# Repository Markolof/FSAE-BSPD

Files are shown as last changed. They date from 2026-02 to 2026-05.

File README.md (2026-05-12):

BSPD with SCS — MES Racing
Rev 2.0 | Formula Student Rule Compliant
Brake System Plausibility Device with Short Circuit Sense. Opens the shutdown circuit if brake and motor current are simultaneously active for more than 0.5 seconds.
Key ICs

LM293 × 4 — comparators (brake & current thresholds)
NE555 — 0.5s timing
SN74HC27 — fault logic
LM358 — buffering
uA7805 — 5V regulation

Adjustable Thresholds
RV1/RV2 — brake | RV3/RV4/RV5 — current

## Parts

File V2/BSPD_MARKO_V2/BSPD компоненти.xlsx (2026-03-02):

v C1, C2, C11, C14, C18 | 5 | 10n | https://www.loging.mk/1478/197583/0/ShowProduct/Kondenzator |  | 110
C1 | 1 | 10n
C2 | 1 | 10n
C11 | 1 | 10n
C14 | 1 | 10n
C18 | 1 | 10n
C3 | 1 | 330n | https://www.loging.mk/1478/169780/0/ShowProduct/Kondenzator_ |  | 13
C4 | 1 | 100n | https://www.loging.mk/1478/197581/0/ShowProduct/Kondenzator |  | 140
> C5, C6, C9, C13, C15, C16 | 6 | 100n
> C7, C8 | 2 | 15p | https://www.loging.mk/1479/199631/0/ShowProduct/Keramichki_Kondenzator |  | 10
C10 | 1 | 15u | https://www.loging.mk/1207/172544/0/ShowProduct/Tantal_Kondenzator_ |  | 47
> C12, C17 | 2 | 10u | https://www.loging.mk/1476/167584/0/ShowProduct/Elektrolitski_Kondenzator_ |  | 28
D1 | 1 | B120-E3 | https://www.loging.mk/1354/162240/0/ShowProduct/Dioda |  | 3
D2 | 1 | 1N4148 | https://www.loging.mk/1354/162242/0/ShowProduct/Dioda |  | 2
> D3-D5 | 3 | 1N5822 | https://www.loging.mk/1548/166237/0/ShowProduct/Shotki_Dioda |  | 18
D7 | 1 | 1N4007 | https://www.loging.mk/1354/162240/0/ShowProduct/Dioda |  | 3
D8 | 1 | CDBA340-HF | https://www.loging.mk/1548/166237/0/ShowProduct/Shotki_Dioda |  | 18
> H1-H4 | 4 | MountingHole
> H5-H8 | 4 | MountingHole
J1 | 1 | ED555_8DS |  | Сликај од старо BSPD терминали за заштрафување
> J2-J4 | 3 | Conn_01x01_Pin |  | Сликај од старо BSPD терминали за заштрафување
J5 | 1 | Conn_01x01_Pin |  | Сликај од старо BSPD терминали за заштрафување
K1 | 1 | SANYOU_SRD_Form_C |  | https://www.loging.mk/1429/173069/0/ShowProduct/Rele | 145
Q1 | 1 | PMOS | https://www.loging.mk/1391/176659/0/ShowProduct/P-Kanalen__MOSFET |  | 215
> R1, R2, R19, R27, R34, R39 | 6 | 1k | https://www.loging.mk/1486/187132/0/ShowProduct/Otpornik_2W |  | 30
> R3, R4, R7, R9, R11, R16, R17, R21, R22, R24, R26, R29, R30 | 13 | 100k | https://www.loging.mk/1482/194923/0/ShowProduct/Otpornik_1_2W |  | 39
> R5, R6, R23, R31 | 4 | 51k | https://www.loging.mk/1483/186442/0/ShowProduct/Otpornik_1_4W |  | 4
> R8, R10, R12-R15, R18, R25, R28, R32, R33, R35-R37 | 14 | 10k | https://www.loging.mk/1484/185622/0/ShowProduct/Otpornik_1_4W |  | 28
R20 | 1 | 910k | https://www.loging.mk/1484/186593/0/ShowProduct/Otpornik_1_4W |  | 2
> RV1-RV5 | 5 | 100k | https://www.loging.mk/1484/186875/0/ShowProduct/Otpornik_1_4W |  | 10
> TP1, TP4 | 2 | TestPoint
U1 | 1 | uA7805 | https://www.loging.mk/1590/164528/0/ShowProduct/Regulator_na_Napon_ |  | 25
> U2-U4, U6 | 4 | LM293_COMP | https://www.loging.mk/1582/163629/0/ShowProduct/Operaciski_Zasiluvach_ |  | 80
U5 | 1 | SN74HC27NE4 | https://www.loging.mk/1594/168179/0/ShowProduct/NILI_Porta |  | 42
U7 | 1 | NE555N | https://www.loging.mk/1567/163760/0/ShowProduct/RC_Tajmer_ |  | 25
ВКУПНО |  |  |  |  | 1037

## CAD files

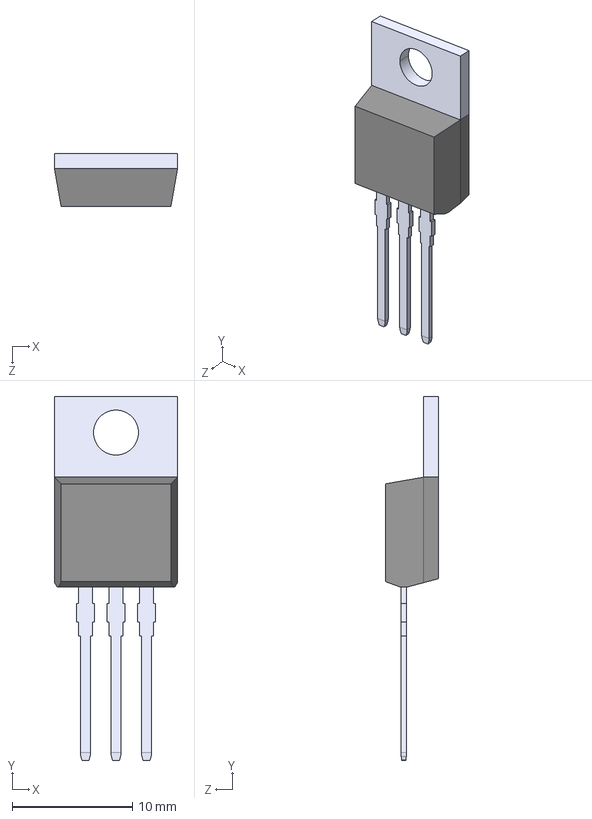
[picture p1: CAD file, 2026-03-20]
BSPD_MES_RACING_V3/Snapeda downloads/IRF9540/IRF9540.step
10.2 x 30.3 x 4.44 mm

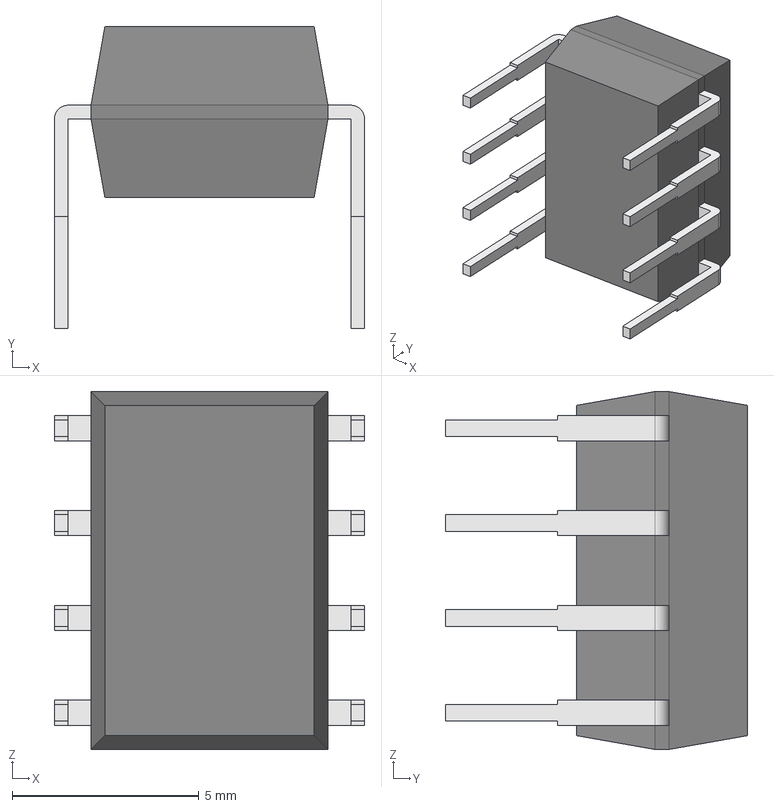
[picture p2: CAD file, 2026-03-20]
BSPD_MES_RACING_V3/Snapeda downloads/LM358N_NOPB/LM358N_NOPB.step
8.31 x 8.08 x 9.59 mm
Body001 (Mirror #1) x 5

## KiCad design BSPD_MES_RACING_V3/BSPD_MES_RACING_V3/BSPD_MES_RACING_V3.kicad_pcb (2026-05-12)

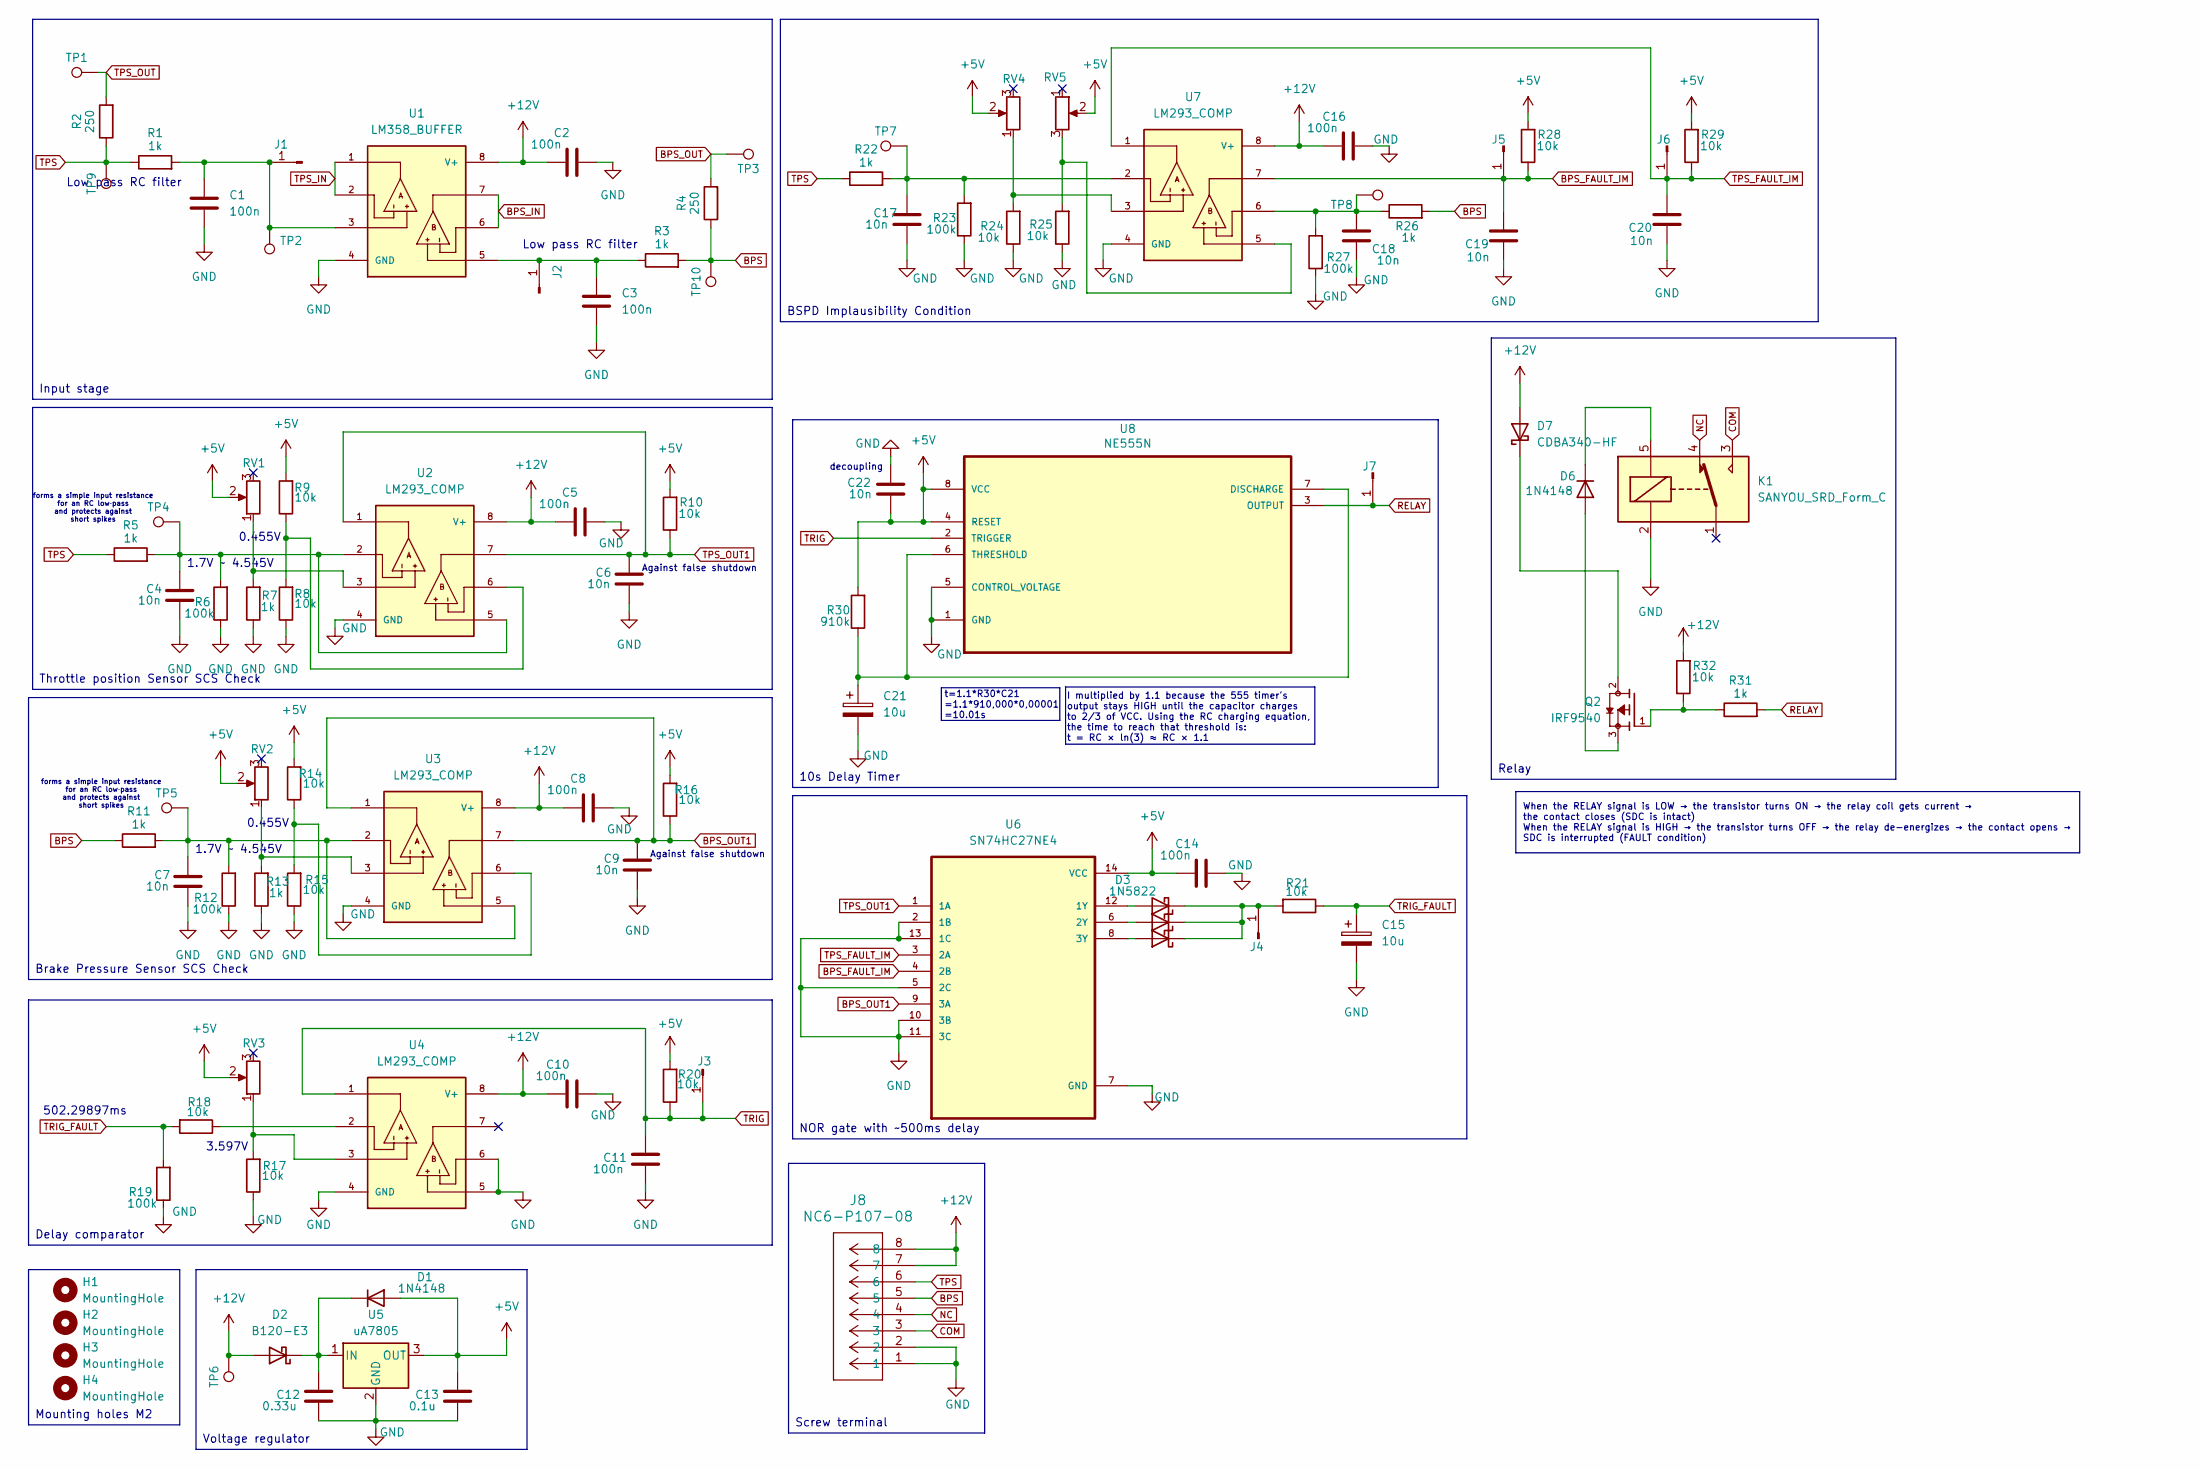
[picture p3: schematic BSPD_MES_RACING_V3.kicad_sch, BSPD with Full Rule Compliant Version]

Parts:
C1, C2, C3, C5, C8, C10, C11, C14, C16: 100n; Resonator-2Pin_W7.0mm_H2.5mm
C4, C6, C7, C9, C17, C18, C19, C20, C22: 10n; Resonator-2Pin_W7.0mm_H2.5mm
C12: 0.33u; Resonator-2Pin_W7.0mm_H2.5mm
C13: 0.1u; Resonator-2Pin_W7.0mm_H2.5mm
C15, C21: 10u; CP_Radial_D8.0mm_P5.00mm
D1, D6: 1N4148; D_DO-35_SOD27_P7.62mm_Horizontal
D2: B120-E3; D_DO-201AE_P15.24mm_Horizontal
D3, D4, D5: 1N5822; D_DO-201AD_P15.24mm_Horizontal
D7: CDBA340-HF; D_DO-201AE_P15.24mm_Horizontal
H1, H2, H3, H4: MountingHole; MountingHole_2.2mm_M2
J1, J2, J3, J4, J5, J6, J7: Conn_01x01_Pin; PinHeader_1x01_P2.54mm_Vertical
J8: NC6-P107-08; CONN8_NC6-P107-08_TEC
K1: SANYOU_SRD_Form_C; Relay_SPDT_SANYOU_SRD_Series_Form_C
Q2: IRF9540; TO254P1052X465X1989-3; PARTREV B
R1, R3, R5, R7, R11, R13, R22, R26, R31: 1k; R_Axial_DIN0207_L6.3mm_D2.5mm_P10.16mm_Horizontal
R2, R4: 250; R_Axial_DIN0207_L6.3mm_D2.5mm_P10.16mm_Horizontal
R6, R12, R19, R23, R27: 100k; R_Axial_DIN0207_L6.3mm_D2.5mm_P10.16mm_Horizontal
R8, R9, R10, R14, R15, R16, R17, R18, R20, R21, R24, R25, R28, R29, R32: 10k; R_Axial_DIN0207_L6.3mm_D2.5mm_P10.16mm_Horizontal
R30: 910k; R_Axial_DIN0207_L6.3mm_D2.5mm_P10.16mm_Horizontal
RV1, RV2, RV3, RV4, RV5: 100k; Potentiometer_Bourns_3266Y_Vertical
TP1, TP2, TP3, TP4, TP5, TP6, TP7, TP8, TP9, TP10: TestPoint; TestPoint_Pad_4.0x4.0mm
U1: LM358_BUFFER; DIP794W45P254L959H508Q8
U2, U3, U4, U7: LM293_COMP; DIP794W45P254L959H508Q8
U5: uA7805; TO-220-3_Horizontal_TabDown
U6: SN74HC27NE4; CERDIP-14_W7.62mm_SideBrazed_LongPads_Socket
U8: NE555N; CERDIP-8_W7.62mm_SideBrazed_LongPads_Socket; MPN NE555N

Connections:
+5V: C13.2, C14.1, C22.2, D1.2 (A), R9.2, R10.2, R14.2, R16.2, R20.2, R28.2, R29.2, R30.2, RV1.2, RV2.2, RV3.2, RV4.2, RV5.2, U5.3 (OUT), U6.14 (VCC), U8.4 (RESET), U8.8 (VCC)
+12V: C2.1, C5.1, C8.1, C10.1, C16.1, D2.2 (A), D7.2 (A), J8.7, J8.8, R32.2, TP6.1, U1.8 (V+), U2.8 (V+), U3.8 (V+), U4.8 (V+), U7.8 (V+)
BPS: J8.5, R3.2, R4.1, R11.1, R26.2, TP10.1
BPS_FAULT_IM: C19.1, J5.1, R28.1, U6.4 (2B), U7.7
BPS_IN: U1.6, U1.7
BPS_OUT: R4.2, TP3.1
BPS_OUT1: C9.1, R16.1, U3.1, U3.7, U6.9 (3A)
COM: J8.3, K1.3
GND: C1.2, C2.2, C3.2, C4.2, C5.2, C6.2, C7.2, C8.2, C9.2, C10.2, C11.1, C12.1, C13.1, C14.2, C15.2, C16.2, C17.2, C18.2, C19.2, C20.2, C21.2, C22.1, J8.1, J8.2, K1.2, R6.1, R7.1, R8.1, R12.1, R13.1, R15.1, R17.1, R19.1, R23.1, R24.1, R25.1, R27.1, U1.4 (GND), U2.4 (GND), U3.4 (GND), U4.4 (GND), U4.5, U4.6, U5.2 (GND), U6.2 (1B), U6.5 (2C), U6.7 (GND), U6.10 (3B), U6.11 (3C), U6.13 (1C), U7.4 (GND), U8.1 (GND), U8.5 (CONTROL_VOLTAGE)
NC: J8.4, K1.4
unnamed: C4.1, R5.2, R6.2, TP4.1, U2.2, U2.5
unnamed: C7.1, R11.2, R12.2, TP5.1, U3.2, U3.5
unnamed: C17.1, R22.2, R23.2, TP7.1, U7.2
unnamed: C18.1, R26.1, R27.2, TP8.1, U7.6
unnamed: C12.2, D1.1 (K), D2.1 (K), U5.1 (IN)
unnamed: D3.2 (A), U6.12 (1Y)
unnamed: D3.1 (K), D4.1 (K), D5.1 (K), J4.1, R21.2
unnamed: D4.2 (A), U6.6 (2Y)
unnamed: D5.2 (A), U6.8 (3Y)
unnamed: D6.2 (A), Q2.3
unnamed: D6.1 (K), K1.5
unnamed: D7.1 (K), Q2.2
unnamed: C1.1, J1.1, R1.2, TP2.1, U1.3
unnamed: C3.1, J2.1, R3.1, U1.5
unnamed: Q2.1, R31.1, R32.1
unnamed: R7.2, RV1.1, U2.3
unnamed: R8.2, R9.1, U2.6
unnamed: R13.2, RV2.1, U3.3
unnamed: R14.1, R15.2, U3.6
unnamed: R17.2, RV3.1, U4.3
unnamed: R18.1, U4.2
unnamed: R24.2, RV4.1, U7.3
unnamed: R25.2, RV5.3, U7.5
unnamed: C21.1, R30.1, U8.6 (THRESHOLD), U8.7 (DISCHARGE)
RELAY: J7.1, R31.2, U8.3 (OUTPUT)
TPS: J8.6, R1.1, R2.1, R5.1, R22.1, TP9.1
TPS_FAULT_IM: C20.1, J6.1, R29.1, U6.3 (2A), U7.1
TPS_IN: U1.1, U1.2
TPS_OUT: R2.2, TP1.1
TPS_OUT1: C6.1, R10.1, U2.1, U2.7, U6.1 (1A)
TRIG: C11.2, J3.1, R20.1, U4.1, U8.2 (TRIGGER)
TRIG_FAULT: C15.1, R18.2, R19.2, R21.1

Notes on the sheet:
3.597V
When the RELAY signal is LOW → the transistor turns ON → the relay coil gets current → the contact closes (SDC is intact) When the RELAY signal is HIGH → the transistor turns OFF → the relay de-energizes → the contact opens → SDC is interrupted (FAULT condition)
forms a simple input resistance for an RC low‑pass and protects against short spikes
502.29897ms
0.455V
Low pass RC filter
I multiplied by 1.1 because the 555 timer's output stays HIGH until the capacitor charges to 2/3 of VCC. Using the RC charging equation, the time to reach that threshold is: t = RC × ln(3) ≈ RC × 1.1
Against false shutdown
t=1.1*R30*C21 =1.1*910,000*0,00001 =10.01s
1.7V ~ 4.545V
decoupling
Relay
NOR gate with ~500ms delay
Screw terminal
Brake Pressure Sensor SCS Check
Throttle position Sensor SCS Check
Input stage
10s Delay Timer
BSPD Implausibility Condition
Voltage regulator
Mounting holes M2
Delay comparator

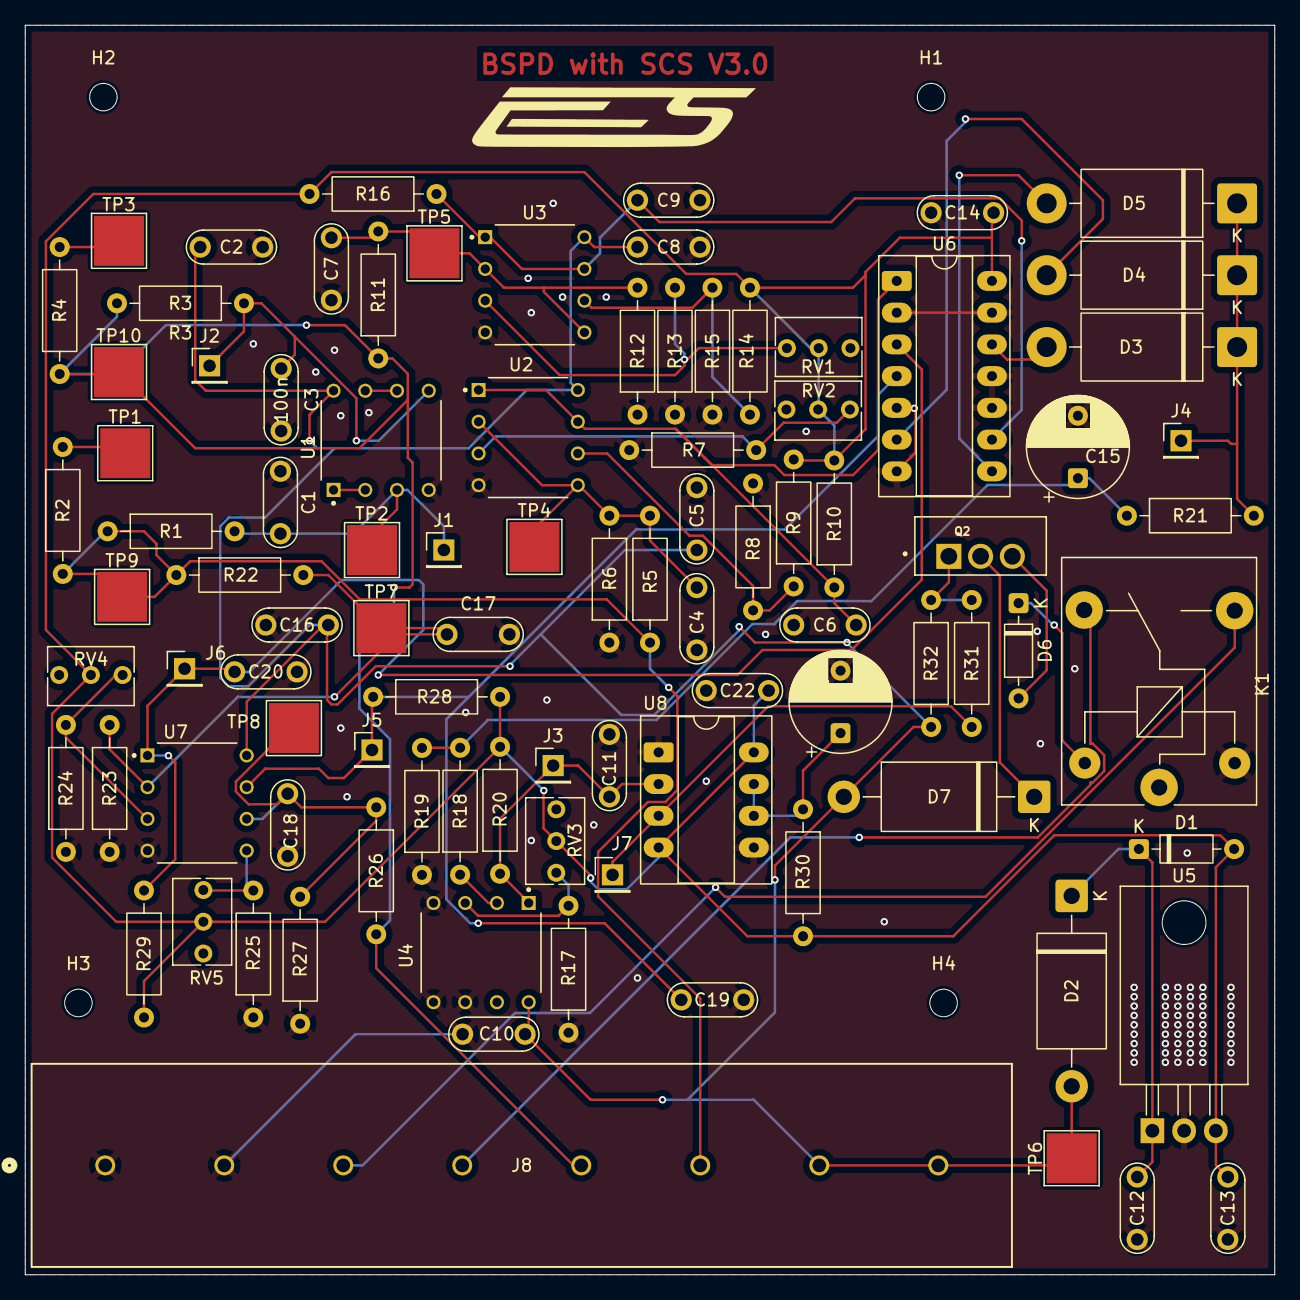
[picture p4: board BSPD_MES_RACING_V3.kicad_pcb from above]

Board: 2 copper layers, 100.0 x 100.0 mm, 98 parts (0 on the bottom side), 42 nets.

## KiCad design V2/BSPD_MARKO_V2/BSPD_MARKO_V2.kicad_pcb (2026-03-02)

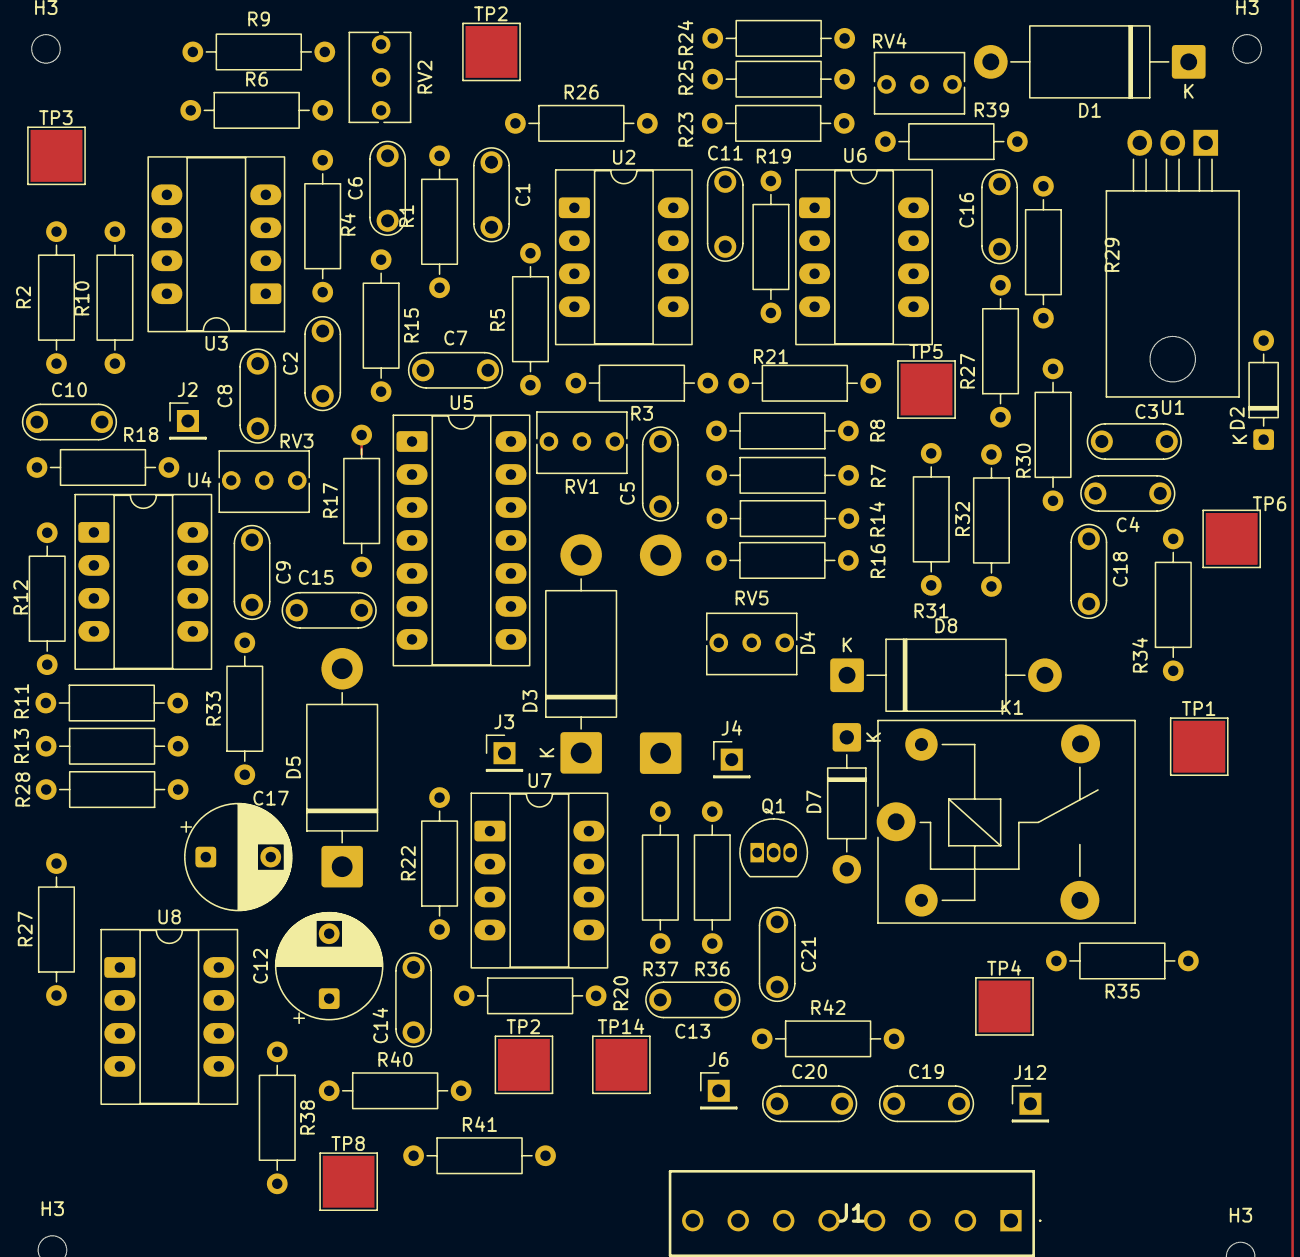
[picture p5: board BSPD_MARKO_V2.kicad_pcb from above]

Board: 2 copper layers, 105 parts (1 on the bottom side), 43 nets.

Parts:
C1, C2, C11, C14, C18: 10n; Resonator-2Pin_W7.0mm_H2.5mm
C3: 0.33u; Resonator-2Pin_W7.0mm_H2.5mm
C4: 0.1u; Resonator-2Pin_W7.0mm_H2.5mm
C5, C6, C9, C13, C15, C16, C19, C20, C21: 100n; Resonator-2Pin_W7.0mm_H2.5mm
C7, C8: 15p; Resonator-2Pin_W7.0mm_H2.5mm
C10: 15u; Resonator-2Pin_W7.0mm_H2.5mm
C12, C17: 10u; CP_Radial_D8.0mm_P5.00mm
D1: B120-E3; D_DO-201AE_P15.24mm_Horizontal
D2: 1N4148; D_DO-35_SOD27_P7.62mm_Horizontal
D3, D4, D5: 1N5822; D_DO-201AD_P15.24mm_Horizontal
D7: 1N4007; D_DO-41_SOD81_P10.16mm_Horizontal
D8: CDBA340-HF; D_DO-201AE_P15.24mm_Horizontal
H3, H3#2, H3#3, H3#4: MountingHole; MountingHole_2.2mm_M2
J1: ED555_8DS; ED5558DS
J2: 01x01P; PinHeader_1x01_P2.54mm_Vertical
J3, J4: Conn_01x01_Pin; PinHeader_1x01_P2.54mm_Vertical
J6, J12: 01x01_Pin; PinHeader_1x01_P2.54mm_Vertical
K1: SANYOU_SRD_Form_C; Relay_SPDT_SANYOU_SRD_Series_Form_C
Q1: 2N3904; TO-92_Inline
R1, R2, R19, R27#2, R34, R38, R39, R42: 1k; R_Axial_DIN0207_L6.3mm_D2.5mm_P10.16mm_Horizontal
R3, R4, R7, R9, R11, R16, R17, R21, R22, R24, R26, R27, R29, R30: 100k; R_Axial_DIN0207_L6.3mm_D2.5mm_P10.16mm_Horizontal
R5, R6, R23, R31: 51k; R_Axial_DIN0207_L6.3mm_D2.5mm_P10.16mm_Horizontal
R8, R10, R12, R13, R14, R15, R18, R25, R28, R32, R33, R35, R36, R37: 10k; R_Axial_DIN0207_L6.3mm_D2.5mm_P10.16mm_Horizontal
R20: 910k; R_Axial_DIN0207_L6.3mm_D2.5mm_P10.16mm_Horizontal
R40, R41: 250; R_Axial_DIN0207_L6.3mm_D2.5mm_P10.16mm_Horizontal
RV1, RV2, RV3, RV4, RV5: 100k; Potentiometer_Bourns_3266Y_Vertical
TP1, TP2, TP2#2, TP3, TP4, TP6, TP8, TP14: TestPoint; TestPoint_Pad_4.0x4.0mm
TP5: TP; TestPoint_Pad_4.0x4.0mm
U1: uA7805; TO-220-3_Horizontal_TabDown
U2, U3, U4, U6, U8: LM293_COMP; CERDIP-8_W7.62mm_SideBrazed_LongPads_Socket
U5: SN74HC27NE4; CERDIP-14_W7.62mm_SideBrazed_LongPads_Socket
U7: NE555N; CERDIP-8_W7.62mm_SideBrazed_LongPads_Socket

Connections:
+5V: C4.1, C13.2, C15.1, D2.2 (A), R7.1, R9.1, R14.1, R15.1, R18.1, R20.1, R22.1, R24.1, R27#2.1, R29.1, R33.2, R39.1, RV1.2, RV2.2, RV3.2, RV4.2, RV5.2, U1.3 (OUT), U5.14 (VCC), U7.4 (RESET), U7.8 (VCC)
BPS: J1.5, R1.2, R34.1, R40.1, R42.2
BPS1_OUT: C7.1, R14.2, R16.2, U2.1, U2.7, U5.1 (1A)
BPS_IN: U8.6, U8.7
BSPD_BPS_F: R27#2.2, U5.4 (2B), U6.7
BSPD_TPS_F: R26.2, R39.2, U5.3 (2A), U6.1
GND: C1.2, C2.2, C3.2, C4.2, C5.2, C6.2, C7.2, C8.2, C9.2, C10.2, C11.2, C12.2, C13.1, C14.1, C15.2, C16.2, C17.2, C18.2, C19.1, C20.2, C21.1, J1.1, J1.2, Q1.1 (E), R3.2, R4.2, R5.2, R6.2, R8.2, R10.2, R11.2, R13.2, R21.2, R23.2, R25.2, R30.2, R31.2, R32.2, R36.1, TP4.1, U1.2 (GND), U2.4 (GND), U3.4 (GND), U4.4 (GND), U4.5, U4.6, U5.2 (1B), U5.5 (2C), U5.7 (GND), U5.10 (3B), U5.11 (3C), U5.13 (1C), U6.4 (GND), U7.1 (GND), U8.4 (GND)
NO: C5.1, C6.1, C9.1, C16.1, C20.1, D1.2 (A), D8.2 (A), J1.4, J1.7, J1.8, K1.4, TP1.1, U2.8 (V+), U3.8 (V+), U4.8 (V+), U6.8 (V+), U8.8 (V+)
unnamed: C1.1, R1.1, R3.1, TP2#2.1, U2.2, U2.5
unnamed: C2.1, R2.1, R4.1, TP3.1, U3.2, U3.5
unnamed: C11.1, R19.1, R21.1, R26.1, TP5.1, U6.3
unnamed: C18.1, R27.1, R32.1, R34.2, TP6.1, U6.5
unnamed: C3.1, D1.1 (K), D2.1 (K), U1.1 (IN)
unnamed: D3.2 (A), U5.8 (3Y)
unnamed: D3.1 (K), D4.1 (K), D5.1 (K), J3.1, R28.1
unnamed: D4.2 (A), U5.12 (1Y)
unnamed: D5.2 (A), U5.6 (2Y)
unnamed: D7.2 (A), K1.2, R35.2
unnamed: D7.1 (K), D8.1 (K), K1.5
unnamed: C21.2, J6.1, R42.1, U8.5
unnamed: C19.2, J12.1, R38.2, TP8.1, U8.3
unnamed: R36.2, R37.2
unnamed: R7.2, R8.1, U2.6
unnamed: R9.2, R10.1, U3.6
unnamed: R12.2, U4.2
unnamed: R13.1, RV3.1, U4.3
unnamed: R5.1, R16.1, RV1.1, U2.3
unnamed: R6.1, R17.1, RV2.1, U3.3
unnamed: R23.1, RV4.1, U6.2
unnamed: R24.2, R25.1
unnamed: R29.2, R30.1
unnamed: R31.1, RV5.1, U6.6
unnamed: R40.2, TP2.1
unnamed: C14.2, U7.5 (CONTROL_VOLTAGE)
unnamed: C12.1, R20.2, U7.6 (THRESHOLD), U7.7 (DISCHARGE)
Rel: J4.1, R37.1, U7.3 (OUTPUT)
SC: J1.3, K1.1
TPS: J1.6, R2.2, R19.2, R38.1, R41.1
TPS1_OUT: C8.1, R15.2, R17.2, U3.1, U3.7, U5.9 (3A)
TPS_IN: U8.1, U8.2
TPS_OUT: R41.2, TP14.1
Trig: C10.1, J2.1, R18.2, U4.1
Trig_Fault: C17.1, Q1.3 (C), R11.1, R12.1, R22.2, R28.2, R33.1, U7.2 (TRIGGER)
